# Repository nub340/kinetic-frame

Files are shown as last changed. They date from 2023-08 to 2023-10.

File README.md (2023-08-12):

# Kinetic Frame

## Description
This is an open-source project for building a kinetic art frame. 

The "shredder" variant, mimics the infamous stunt Banksy pulled off at a Sotheby's auction back in 2018. However, where the original device actually shredded the artwork contained within the frame, this one is an illusion. While it really <em>looks</em> like the artwork inside is being shredded, it's actually an artful deception. In reality, a separate pre-shredded copy of the artwork is concealed within the frame, which is cleverly lowered from the bottom of the device while the displayed artwork smoothly scrolls down and out of view, resulting in a very convincing illusion. The device can then be reset to it's original state so the performance can be enjoyed again and again, indefinitely!

The "scroller" variant, is a simplified version that simply scrolls the artwork in a few different ways: 
- Continuously scrolling - Keep scrolling the same direction, continuously.
- Panning - Slowly scroll all the way down, stop, then all the way back up again, stop, repeat.
- Toggle - switch between two different images

The main artwork needs to be printed onto a 13.5" x 36" canvas belt (or similar). The belt is mounted on rollers that are spun by a stepper motor. The "shredder" variant also requires a second copy of the artwork to be mounted to a clip hung from a fishing line. See the assembly instructions for more details.

## Authors
- [nub340](https://github.com/nub340)

## Status   
Alpha release. This is the "first light" push which has been fully built and tested by the original author 

See [CHANGELOG](CHANGELOG.md) for more details
  
<!-- ## See what it looks like
Describe what sets this apart from related-projects. Linking to another doc or page is OK if this can't be expressed in a sentence or two.

**Screenshot**: If the software has visual components, place a screenshot after the description; e.g.,

![](https://blah.png) -->

## Tech Stack & Requirements 
- Arduino
- C++ code/sketch
- Custom PCBs via JLCPCB
- 3D printed parts
- Manual fabrication

## Tools & Cosumables Needed
- Hack saw or power saw for cutting aluminum tubing
- Heat gun or blow dryer for heat shrink tubing
- Soldering iron & solder (heavy and thin rosin core)
- Wire strippers/cutters
- Pliers/crimper
- 3D printer
- JB Weld for Metal (or similar)
- Fabric glue

## Materials Required
Description | Qty | Qty Type | Note
--- | --- | --- | ---
[Arduino Nano](https://www.amazon.com/LAFVIN-Board-ATmega328P-Micro-Controller-Arduino/dp/B07G99NNXL) | 1 | pieces | Microcontroller. The brain of the whole device.
[NEMA17 Stepper Motor](https://www.amazon.com/gp/product/B00PNEQ79Q) | 1 | pieces | Low profile recommended for compactness
[A4988 Driver](https://www.amazon.com/HiLetgo-Stepstick-Stepper-Printer-Compatible/dp/B07BND65C8) | 1 | pieces | Drives the stepper motor
[12V-to-5V Buck Converter](https://www.amazon.com/gp/product/B08Q3TKJH5) | 1 | pieces | 5V for Arduino, A4988 driver, and other components
[IR Remote & Receiver](https://www.amazon.com/DWEII-Infrared-Wireless-Control-Raspberry/dp/B09ZTZQFP7) | 1 | pieces | Any will work, may need to update [code](./Code/banksy_shredder_frame.ino#L16)
[Buzzer](https://www.amazon.com/gp/product/B01N7NHSY6) | 1 | pieces | Active or passive will work. Use resistor with passive.
[Resistor](https://www.amazon.com/Resistor-Tolerance-Resistors-Limiting-Certificated/dp/B08QRT11GG) | 1 | pieces | Optional for Active buzzer. Passive use 100ohm.
[4-Pin Connectors](https://www.amazon.com/CQRobot-Connector-Terminal-Industrial-Integrated/dp/B0731NHS9R) | 1 | pieces | Optional. Can solder motor wires directly to PCB
[1" Aluminum Tubing](https://www.mkmetal.net/6061-t6rndtube1x.065x12) | 28 | inches | Top & bottom rollers. 1" x .065" (ID: .87" \| 22.1mm)
[Skateboard Bearings](https://www.amazon.com/gp/product/B07S1B3MS6) | 3 | pieces | JB Weld flush into ends of aluminum tube
[ Heat Shrink Tubing](https://www.amazon.com/gp/product/B0B38T8SC1) | 2 | pieces | (1.25" Diameter x 15" Length) X 2. Shrink over aluminum tubes to make rollers.
[Motor mount spool](./STL/motor-mount-spool.stl) | 1 | pieces | 3D print. Connects stepper motor to the upper roller, and provides a spool for the fishing line.
[Fishing line](https://www.amazon.com/Zebco-Quantum-300210-Outcast-Monofilament/dp/B000KKUO8S) | 3 | feet | 10lb+ recommended to minimize stretching
[Eye hook screws](https://www.amazon.com/gp/product/B0899QTFWS) | 2 | pieces | 10x5mm. Fishing line routing.
[Swivel hook](https://www.amazon.com/Dr-Fish-Interlock-Stainless-Corrosion-Resistanc/dp/B07JQBLZQG) | 1 | pieces | Optional. Small size 14. Attach fishing line to clip
[Shredded Artwork Clip](./STL/clip.stl) | 1 | pieces | Holds the shredded artwork inside frame
[Roller mount pins: long](./stl/roller-mount-pin-long.stl) | 3 | pieces | 3D print. Top & bottom rollers are mounted and rotate on these.
[Roller mount pins: short](./stl/roller-mount-pin.stl) | 4 | pieces | 3D print. Rubber bands attachments to provide tension on bottom roller.
[3/4" Canvas Offset Clips](https://www.amazon.com/gp/product/B01MS39JJP) | 4 | pieces | For mounting picture frame to completed PCB box
[12V Power Adapter](https://www.amazon.com/gp/product/B00Q2E5IXW) | 1 | pieces | Minimum 2A for stepper motor. 8ft cord recommended
[Barrel Connector](https://www.amazon.com/gp/product/B074LK7G86) | 1 | pieces | Connection for 12V power adapter
[Paper Mount Boards](https://www.dickblick.com/items/crescent-mounting-board-15-x-20-x-055-ultra-black)  | 2 | pieces | For internal separator and back pieces. [Cut to size](#mount-boards).
[Card Stock](https://www.amazon.com/gp/product/B0773KWZLG) | 1 | pieces | Optional backing. Glue to back of artwork copy before shredding for better support and durability.
[12" x 16" Picture Frame](https://www.etsy.com/listing/630386658/west-frames-elegance-french-ornate) | 1 | pieces | Minimum 1-1/2" Moulding to hide motor & electronics
[Custom PCB: Left & Right](./PCB/Gerber_Left_Right.zip) | 1 | pieces | Order from [JLCPCB](https://jlcpcb.com/)
[Custom PCB: Top, Bottom, & Supports](./PCB/Gerber_Top_Bottom.zip) | 1 | pieces | Order from [JLCPCB](https://jlcpcb.com/)
[Main Artwork Canvas: 13.5" x 36"](https://www.bagsoflove.com/unframed-canvas-photo-prints) | 1 | pieces | The main un-shredded artwork that will be displayed in the frame.
[Shredded Artwork Canvas: 13.5" x 12 - 16"](https://www.bagsoflove.com/unframed-canvas-photo-prints) | 1 | pieces | The shredded artwork that will be lowered from the bottom of the frame. Doesn't have to be full 16" as only around half is ever exposed.

## Getting the Printed Circuit Boards (PCBs) Made
You can have the PCBs made via JLCPCB. They require a minimum of 5 copies of any PCB. Follow the steps below to order:

- Browse to [JLCPCB](https://jlcpcb.com/)
- Click "Instant Quote" button
- Upload [Gerber file for Left & Right](./PCB/Gerber_Left_Right.zip) pieces
- Under the <b>PCB Specifications</b> section, select the following:
    - <b>Different Design</b>: ```2```
    - <b>Delivery Format</b>: ```Panel by Customer```
    - <b>PCB Thickness</b>: ```2.0```
    - <b>PCB Color</b>: <em>Select your desired color</em>
- Click "Save to Cart".
- Repeat for [Top, Bottom, and Supports](./PCB/Gerber_Top_Bottom.zip) Gerber file
    - Only difference is choose <b>Different Design</b>: ```3``` this time
- You will end up with 2 items in your cart. Proceed to checkout when you are ready to place your order.
- You can choose ```1.6``` PCB thickness to save money, but ```2.0``` is way sturdier and recommended.
- <b>NOTE</b>: ```Gerber files are just zip files. Upload the whole zip, no need to extract first.```

## Fabricating the Rollers
You'll need to fabricate the upper & lower rollers from a few components:
- Aluminum tubing
- Skateboard bearings
- Heat shrink tubing
- JB weld for metal/aluminum (marine works well)

Follow these steps:
- Cut the aluminum tubes to length:
    - Upper: ```13-3/4"``` (extra space needed for 3D printed motor mount spool)
    - Lower: ```14"```
- Install bearings:
    - You'll need three bearings total. One for the upper, and two for the lower.
    - Test fit the bearings into the ends of the tubes. Make sure they will fit nice and flush with the ends of the tubes. You may need to sand the inside of the tubes slightly if it's too tight a fit.
    - Remove all three bearings.
    - Install one bearing at a time with the following procedure:
        - Apply/scrape a <em>little bit</em> of JB weld all around the inside perimeter of the tube openings such that when the bearing is pressed in, it will make contact with both the outer bearing race and inner tube wall. 
        - Press bearing into tube end so that it sits nice and flush with the tube end.
        - Don't use too much JB Weld as you don't want it to get onto the inner bearing race.
        - Let the JB Weld harden/cure thoroughly.
        - Ensure the bearing spins freely. See [notes](#bearing-notes) below if not.
- Apply heat shrink:
    - Cut two ~15" lengths of heat shrink tubing and shrink them onto each roller, both upper and lower.
    - Trim the excess heat shrink tubing with a razor blade so that it's perfectly flush with the ends of the tubes and bearings, with no overhang.
- Install 3D printed motor mount spool
    - Press into the tube opening opposite of the bearing of the upper roller tube
    - Ensure that it is fully pressed in and seated so that it grips the tube well.
    - Total length of tube plus motor mount should be 14" 

NOTES:

- If you get JB Weld on the center bearing race and it doesn't want to spin, you can try to use your finger, or stick a large pen or something similar through the hole until it grabs onto the sides of the hole, and then spin the tube to try and break bond and get it spinning freely.
- You might be able to use PVC tubing instead of aluminum, but the PVC might warp when applying the heat shrink tubing.
- If you got the right tubing and skateboard bearings, they should fit right into the ends of the tubes. The outer diameter of the bearings are 22mm, so the inside diameter of the tubes need to be just over 22mm.

## Fabricating the Artwork
The shredder frame requires two separate copies of the same artwork to function. One for the main un-shredded art that will be visible in the frame when in the default/normal state, and one for the shredded piece that is lowered from the frame.

The two artworks can be fabricated in many ways so feel free to experiment with different approaches. If you find one that works well that is not covered here, please write up an addendum ```.md``` and make a pull request for it to be included in the main repository.

I have tried a few different approaches myself and found having the canvas made via a service like [bagsoflove](https://www.bagsoflove.com/unframed-canvas-photo-prints) provides the best results. The artwork is printed directly onto a high quality canvas which looks great, and avoids any issues with the picture starting to come off after repeated times going around the rollers.

Gluing a separate artwork onto a blank piece of canvas or vinyl is another (cheaper) approach, but presents potential peeling issues as it must be able to rotate around the lower roller over and over again. If it starts to peel off, it will inevitably start causing jams. I had decent results using a piece of vinyl instead of canvas and using a high strength 3M spray adhesive.

You can also simply make your own stencils and spray paint directly on a blank canvas, although this might be harder to make two identical copies.

### Main Un-shredded Artwork
- 13.5" x 36" made into a belt/loop
- Mounted on rollers
- Have made
    - https://www.bagsoflove.com/
    - https://www.contrado.com/
    - You'll need to upload a high quality image (i.e. 200 DPI) in the right dimensions.
    - [Example image](./Images/banksy_13.5x52_fiberboard_200DPI.png)
        - Single image contains both the un-shredded (upper) and shredded (lower) artworks in one. 
        - It will be delivered as one big canvas, so you'll need to separate the upper and lower canvases by cutting with scissors or fabric cutter, etc. Cut very precisely along the horizontal dotted line separating the upper and lower portions.
        
        - cut the bottom image out and glue it to cardstock before manually shredding for best results and durability. 
        - Only shred bottom half of shredded artwork canvas.
        - Trim the upper un-shredded artwork canvas so that it's 13-1/2" wide, and ~37" tall. Use high quality fabric glue to make into a belt/loop. You only need about an inch of overlap for glue to make a good bond. 
        - The fiberboard-like background on the upper canvas should loop around and perfectly match with the top to make a perfect 36" long belt. 
- Make yourself
    - Print, Stencil, or Glue artwork onto a 13.5" x 36" canvas about 3/4 of the way down. 
    - Make into a "belt" by gluing the ends together. 
    - Seam should be near the bottom in back when artwork is centered in frame on the rollers. Far enough down so that it never reaches the upper roller when in the fully shredded state.

## Fabricating the Shredded Artwork
Duplicate artwork above. Glue canvas to cardstock for best results, or just use the cardstock. Shred bottom 50% or so. By hand or with a paper shredder you can stop & reverse.

## 3D Printed Parts
- [Motor mount spool](./STL/motor-mount-spool.stl) - Connects the motor to the upper roller. Also provides a spool for the fishing line and acts as a winch for lowering and raising the shredded artwork hidden inside.
- [Roller mount pin: long](./STL/roller-mount-pin-long.stl) - Provides a spindle for the upper & lower rollers to mount and rotate on.
- [Roller mount pin: short](./STL/roller-mount-pin.stl) - Provides an attachment point for the tensioning rubber bands for the lower roller.
- [Artwork clip](./STL/clip.stl) - Provides an attachment point for the shredded artwork to hang from. 

It's recommended to print these components with PETG or PLA @ .15mm or better resolution and 15% infill. Be sure to use the appropriate slicer for your printer. 

## Mount Boards

- Separator: 14.25" x 18.25" 
- Backing: 14.5" x 18.75"
    - bend the bottom slightly so that the shredded artwork is pushed away from the wall a little

## Known issues

Calibration

----

## Open source licensing info
1. [TERMS](TERMS.md)
2. [LICENSE](LICENSE)
3. [CFPB Source Code Policy](https://github.com/cfpb/source-code-policy/)

----

## Credits and references

1. Banksy for his original performance art
2. Creative engineers
3. Arduino

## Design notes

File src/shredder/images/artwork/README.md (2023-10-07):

Images in this folder are intended to be used for printing onto a canvas 13.5" x 52" in size and includes two copies of the same image. Cut them at the seam to make a 36" upper and a 16" lower canvas.

Form the upper 36" canvas into a loop/belt by gluing or sewing the top and bottom together. You want the loop/belt to be 36" in circumference, so don't overlap the actual printed portion. Use the non-printed margin for any overlap. Better yet, sew the two ends butted up against each other with no overlap at all.

It is recommended to glue the lower 16" canvas to cardstock or thick paper for durability and to prevent fraying. You can cut it shorter than 16" but you'll need to adjust the length of the fishing line to compensate.

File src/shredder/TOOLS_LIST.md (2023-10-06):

# Tools, Equipment, and Software List

- Soldering Iron
- 1.5mm Allen Wrench
- Pliers
- Philips Screwdriver
- Computer with Internet Access
- Arduino IDE
- USB Cable (micro or type-C, depends on the Arduino Nano you got)
- 3D Printed 90-Degree Jig

## Consumables
- Solder (thick rosin core)
- Solder (thin rosin core)
- Tape (masking, painters, or scotch)
- Epoxy, JBWeld, Silicone, or Glue

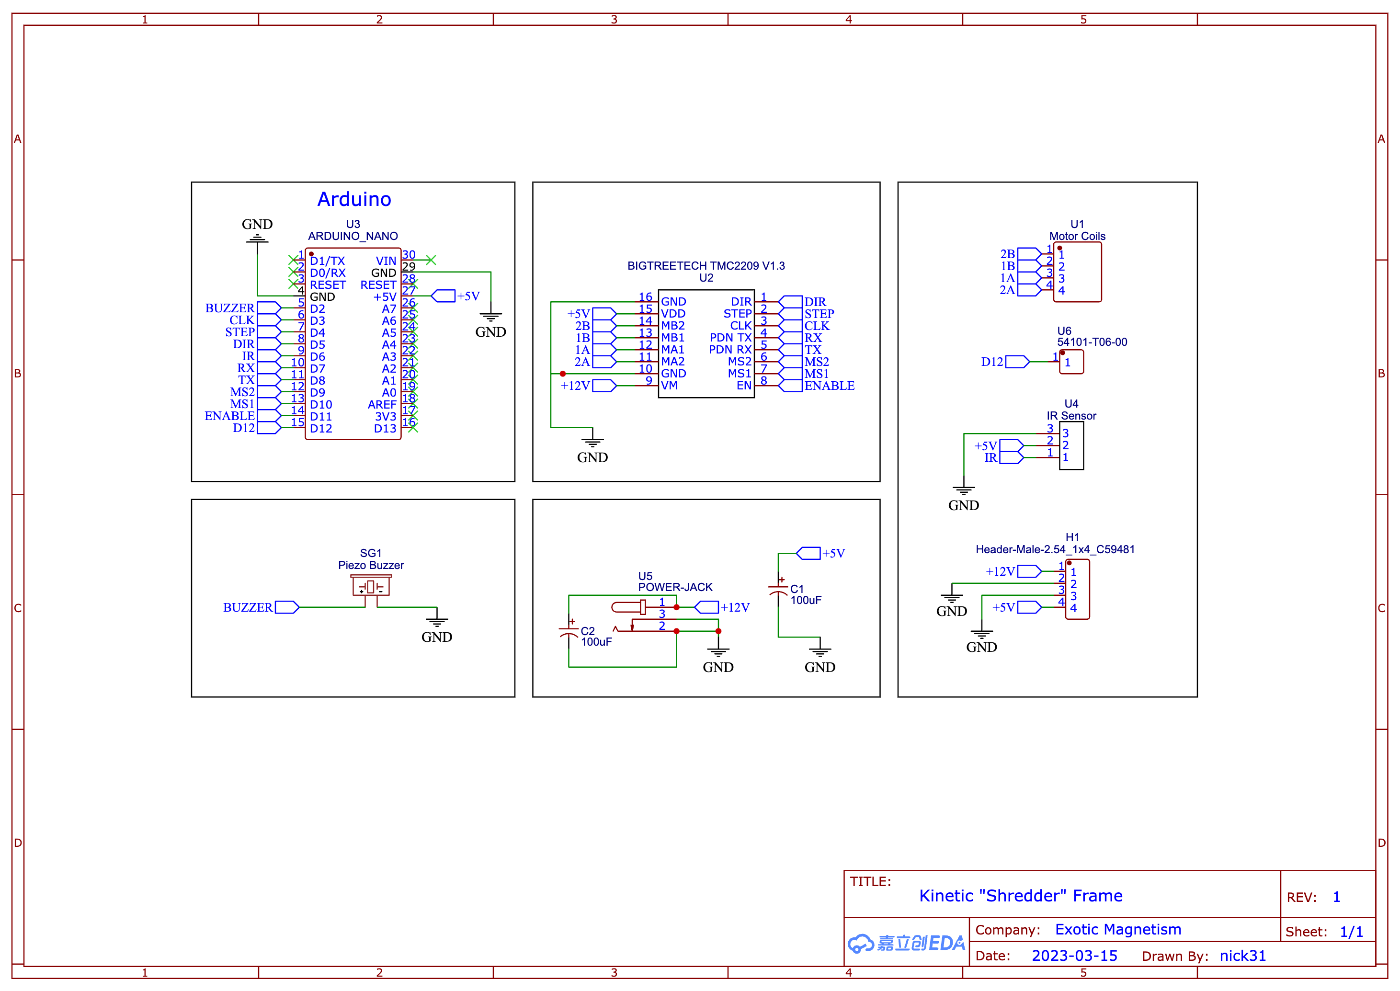
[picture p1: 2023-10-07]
src/shredder/pcb/Schematic_TMC2209.png

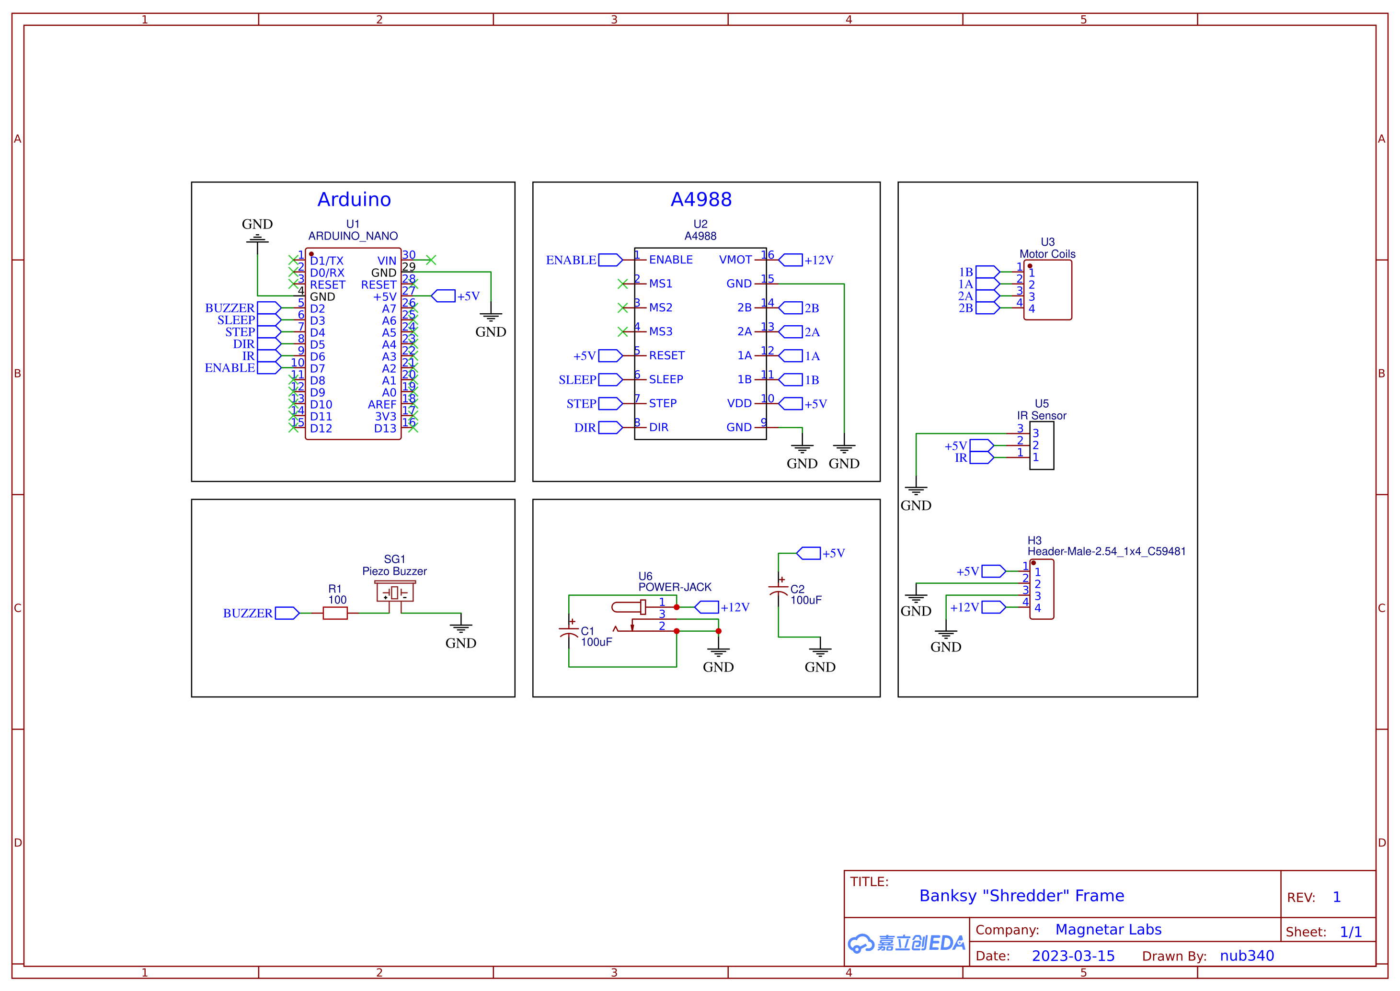
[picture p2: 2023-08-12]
src/shredder/pcb/Schematic_A4988.png

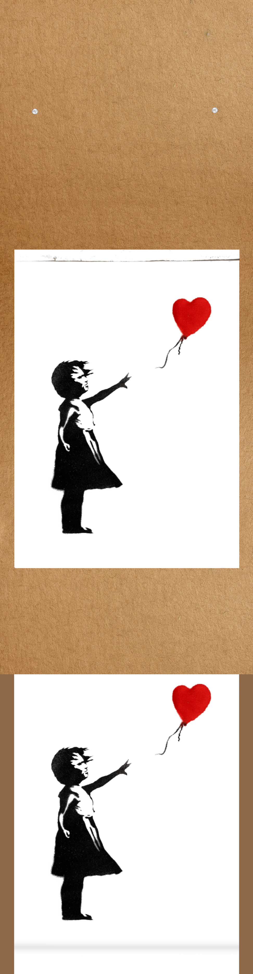
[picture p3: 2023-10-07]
src/shredder/images/artwork/banksy_13.5x52_fiberboard.jpg

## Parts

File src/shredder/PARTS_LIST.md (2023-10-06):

# Parts List

## Structural
- PCB Frame (Left, Right, Top, Bottom)
- Aluminum Tubing (x2)
- Heat Shrink Tubing (x2)
- Flanged Bearings (x3)
- 3D Printed Bearing Mounting Pins (x3)
- 3D Printed Motor Mount
- Eyelets (x3, 1 needed, 2 extra)
- Small Rubber Bands (x8)
- Fishing Line
- Swivel Hooks (x2)
- 3D Printed Hanger
- Art Board (x2)
- Rubber Bands (x8)

## Electronics
- Arduino
- Stepper Motor Driver (A4988 or TMC2209)
- 5V Buck Converter
- 4-pin Header
- IR Receiver
- Piezo Buzzer
- 100uf 16v Capacitors (x2)
- Barrel jack
- Stepper Motor Pigtail

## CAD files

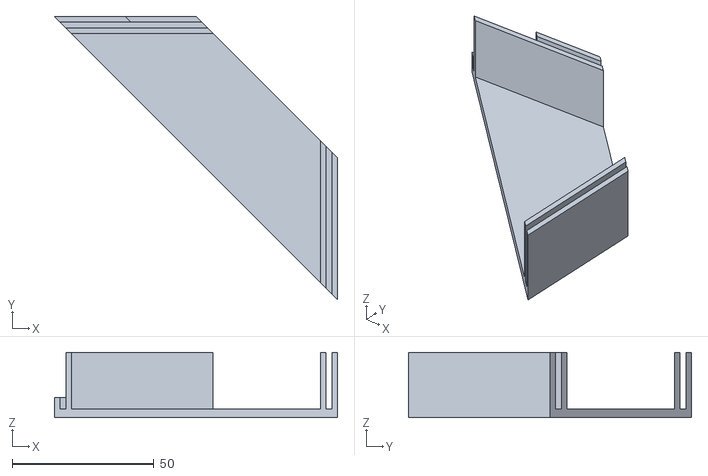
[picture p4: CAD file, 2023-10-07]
src/shredder/3dprint/90degree-jig2.stl
100.0 x 100.0 x 23.0

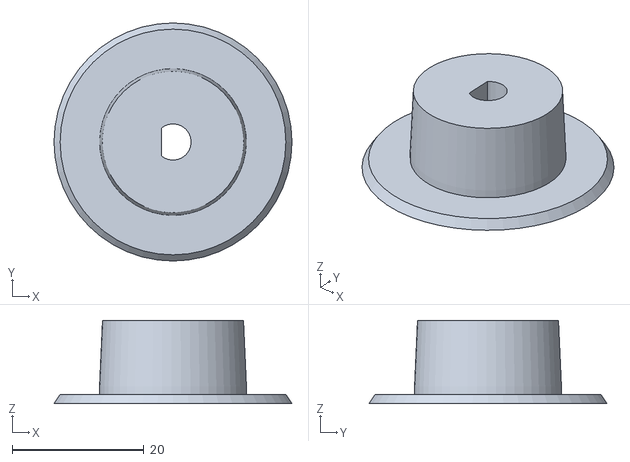
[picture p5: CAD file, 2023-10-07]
src/shredder/3dprint/motor-mount.stl
36.1 x 36.1 x 12.6

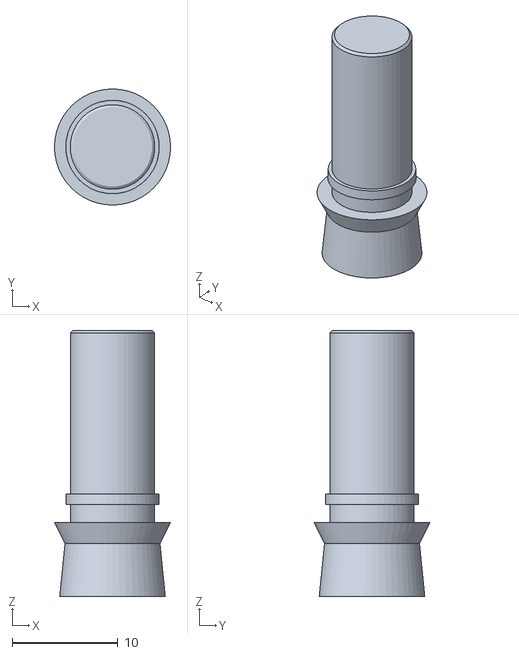
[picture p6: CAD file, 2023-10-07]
src/shredder/3dprint/roller-mounting-pin.stl
11.0 x 11.0 x 25.2

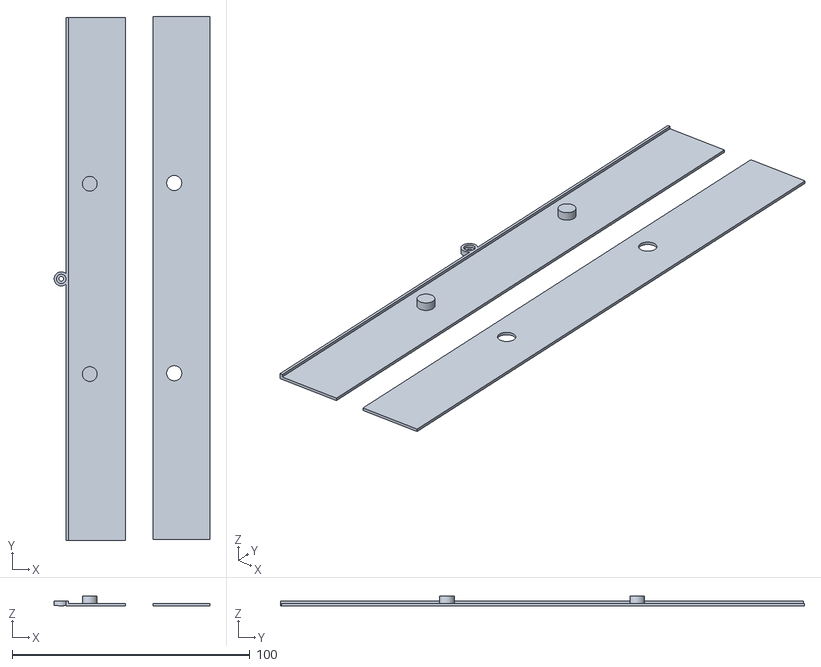
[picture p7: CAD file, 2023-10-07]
src/shredder/3dprint/hanger.stl
65.5 x 220.3 x 4.00

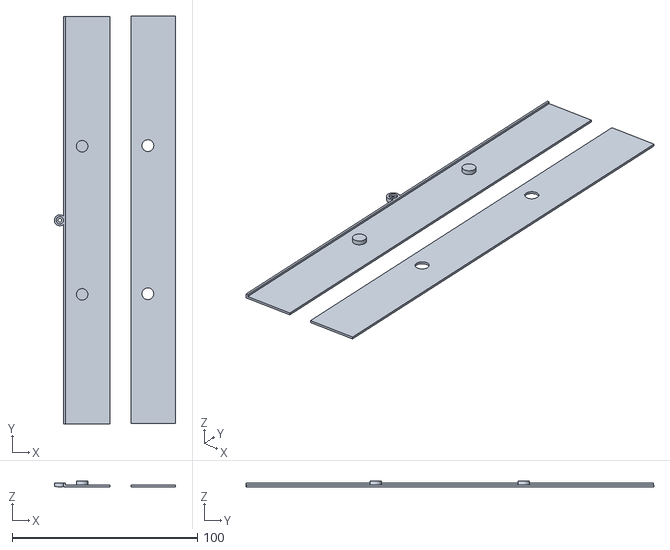
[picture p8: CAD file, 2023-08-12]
src/shredder/3dprint/clip.stl
65.5 x 220.3 x 3.00

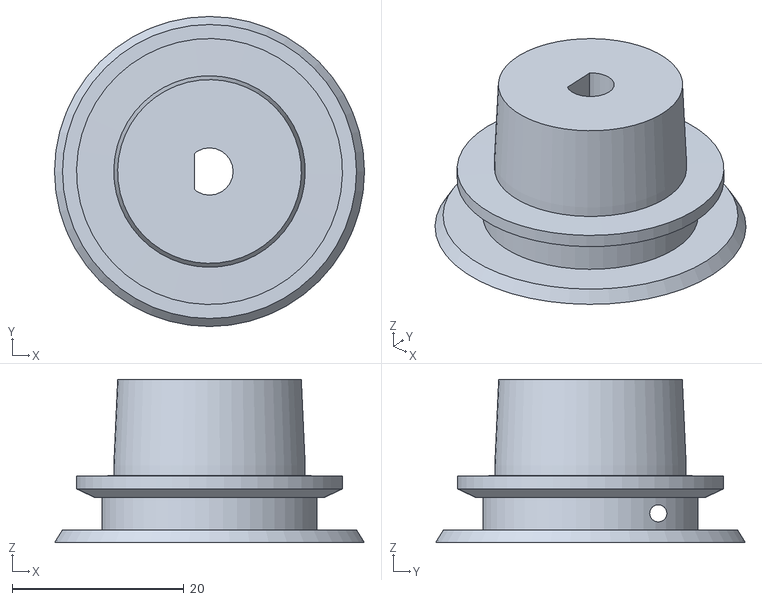
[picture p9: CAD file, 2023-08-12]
src/shredder/3dprint/motor-mount-spool.stl
36.1 x 36.1 x 19.0

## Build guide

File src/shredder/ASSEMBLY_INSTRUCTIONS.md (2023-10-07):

# Kinetic Shredder Frame Kit Assembly Instructions

### Prerequisites
Ensure that you have all of the parts and tools on hand before continuing.

- [Parts](PARTS_LIST.md)
- [Tools](TOOLS_LIST.md)

## 1. Assemble the PCB chassis
Use the included 3D printed jig to position the PCB pieces so their corners meet at a 90 degree angle.

### Tools Required
- 90 Degree Jig
- Soldering Iron
- Solder (thick rosin core)

### Parts Needed
- "Left" PCB
- "Right" PCB
- "Top" PCB
- "Bottom" PCB
- Lateral Support PCBs (x3)

### Steps
- The PCBs come in two panels. Break them apart carefully into their constituent pieces.
- Join the "Left" and "Top" PCB pieces first.
    - Place both pieces in the jig so that the sides marked "Front" are facing the same direction.
    - Carefully bring the corners together so that the tabs interlock and fit together with no gaps and a nice 90 degree angle is achieved.
    - The silver metal strips should be facing each other on in the inside of the corner.
    - Cut a piece of rosin core solder and lay it in the corner on the silver metal strips.
    - Use your soldering iron to melt the solder to join the "Left" and "Top" PCB pieces together.
    - Let it cool before attempting to remove from jig.
- Join the "Left" and "Bottom" PCB pieces
- Join the "Right" and "Top" PCB pieces
- Join the "Right" and "Bottom" PCB pieces
- Install the three lateral support pieces
    - Start with the middle support
    - Use a pice of tape to hold the "Left" and "Right" PCB pieces at the correct distance so that the ends of the middle support are flush with the exterior
    - solder both sides and let cool
    - flip over, solder both sides again and let cool
    - Repeat for the top and bottom lateral supports

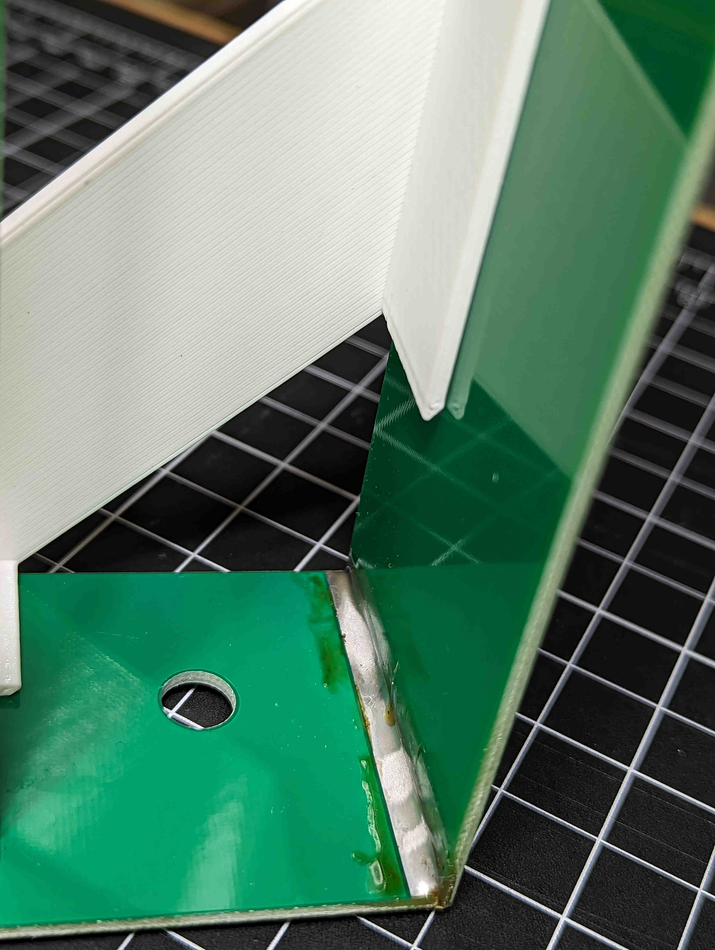
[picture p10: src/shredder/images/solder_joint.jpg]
solder joint

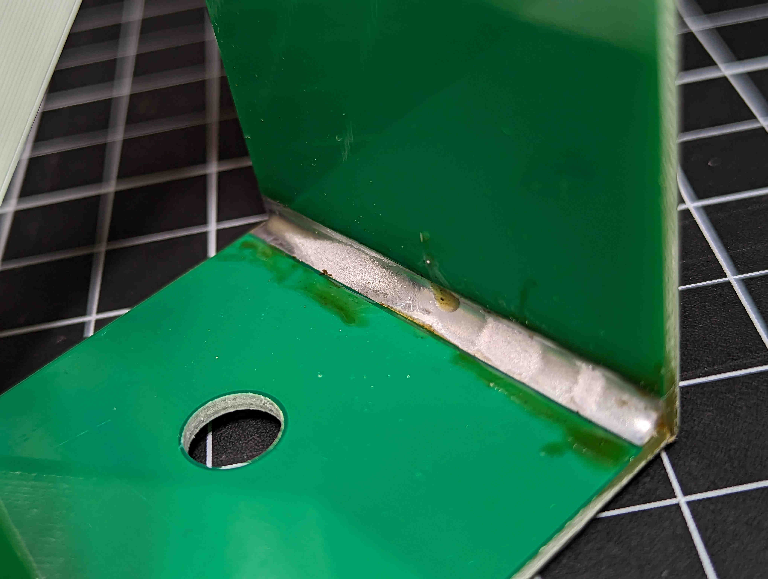
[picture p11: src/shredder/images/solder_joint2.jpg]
solder joint closeup

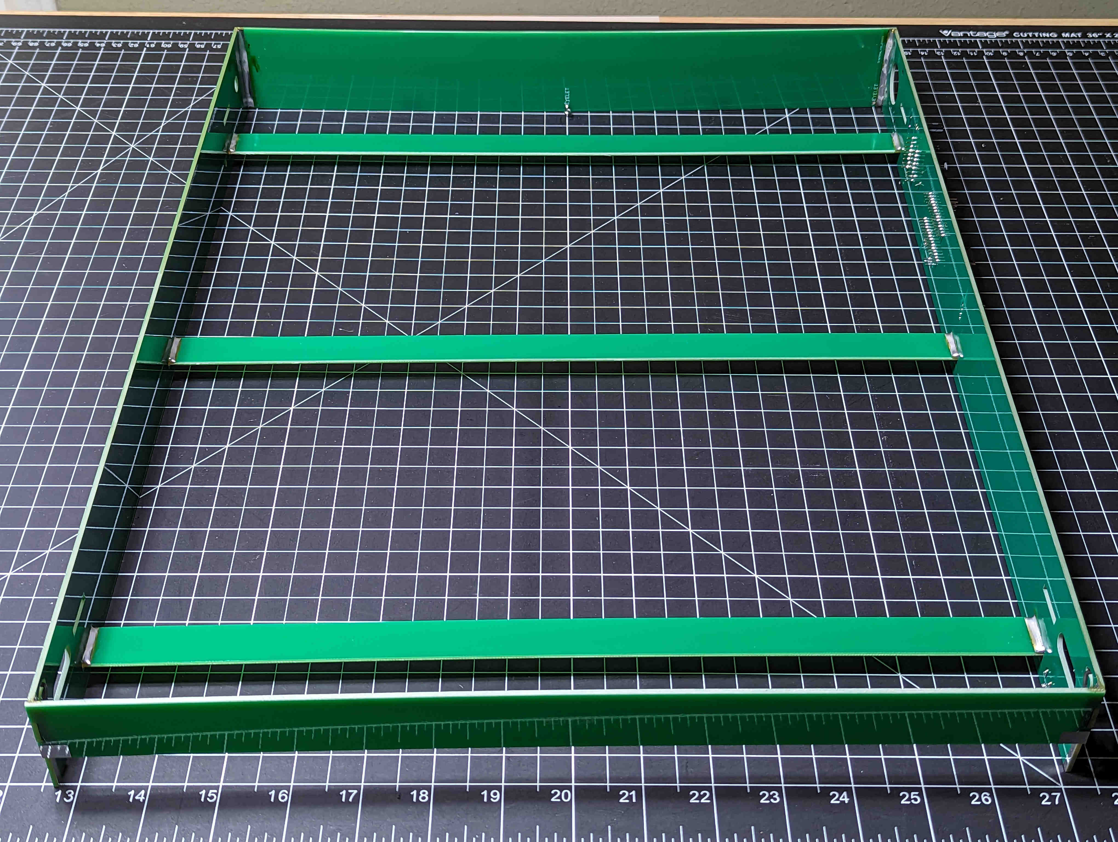
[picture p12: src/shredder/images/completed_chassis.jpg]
completed chassis


## 2. Install the eyelet
The eyelet is used as a pulley of sorts for the fishing line that will hold the pre-shredded image within the chassis.

### Tools Required
- Pliers
- Soldering Iron
- Solder (thin rosin core)

### Parts Needed
- Eyelet
- Chassis

### Steps
- Install the small eyelet into the hole located at the center rear of the "Top" PCB piece.
- The eyelet is fragile and can easily break, so don't screw it in more than one or two turns. Just enough so that it stays in place. It should NOT need to poke through the top. 
- Orient the eyelet hole so that it's facing front & back. 
- Use a dab of solder on top & bottom to secure it in place.

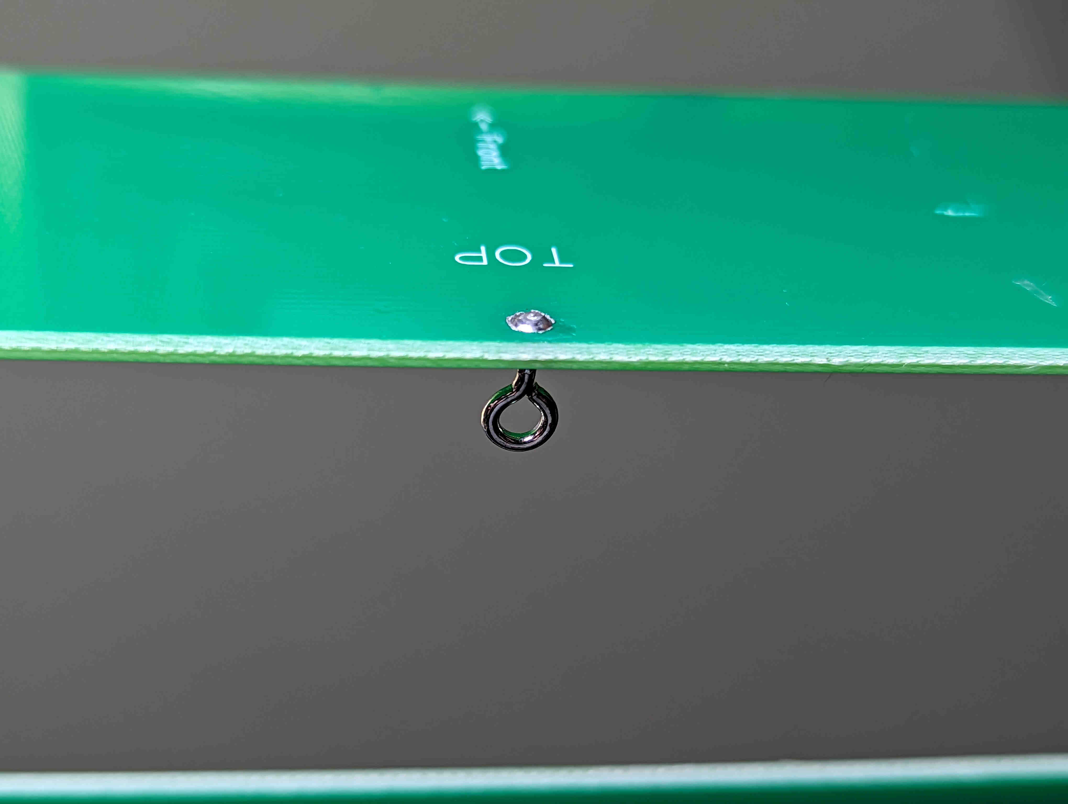
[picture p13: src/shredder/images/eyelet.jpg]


## 3. Solder the Electronics
Install and solder all of the electronic components on the PCB labeled "Right". Be sure to pay attention to the orientation of each component to ensure the pins and polarity are correct.

### Tools Required
- Soldering Iron
- Solder

### Parts Needed
- Arduino
- Stepper Motor Driver (A4988 or TMC2209)
- 5V Buck Converter
- 4-pin Header
- IR Receiver
- Piezo Buzzer
- 100uf 16v Capacitors (x2)
- Barrel jack
- Stepper Motor Pigtail

### Steps
- Arduino 
- Stepper Motor Driver 
- Active Piezo Buzzer 
- Capacitors 
- 12V Barrel Jack
- 4-pin Header
    - Buck Converter goes onto 4-pin Header
    - When oriented correctly, should hang downwards
    - EN pin does not connect to anything
- IR Receiver
- Stepper Motor Pigtail
    - From left to right (front to back): Red, Blue, Green, Black
    - DO NOT INSTALL THE STEPPER MOTOR ITSELF YET

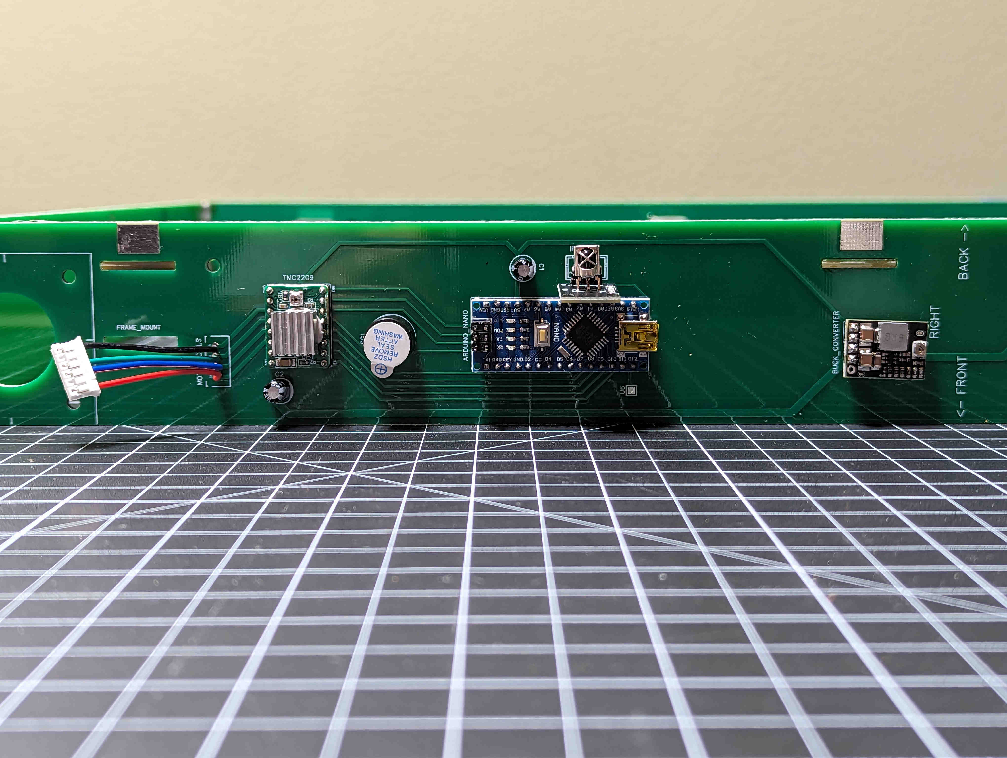
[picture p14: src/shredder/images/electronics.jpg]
electronics

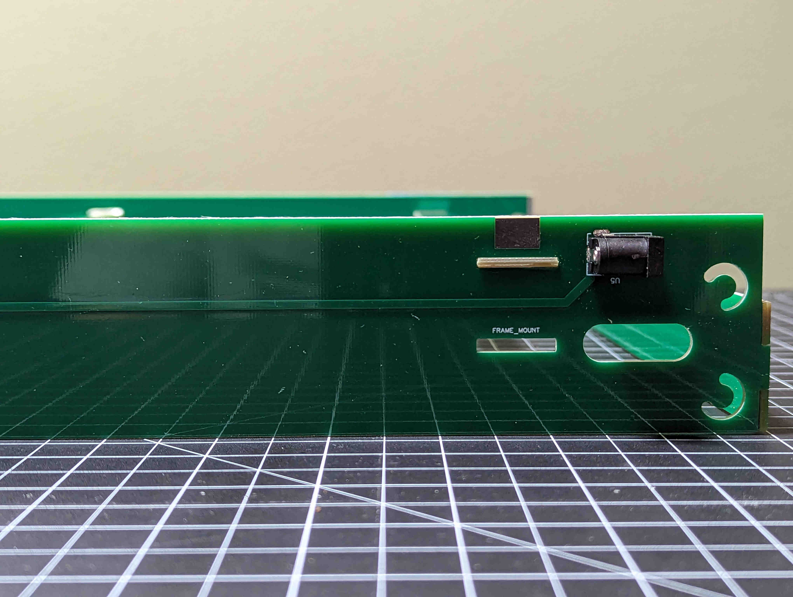
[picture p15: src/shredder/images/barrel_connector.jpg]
barrel connector


## 4. Construct the Rollers
The rollers are made from aluminum tubing and some heat shrink to make a rubberized surface for better grip. Bearings and a motor mount are used in the ends.

### Tools Required
- Heat Gun or Hair Dryer
- Epoxy/JBWeld/Silicone/Glue (optional)

### Parts Needed
- Aluminum Tubes (x2)
- Heat Shrink Tubing (x2)
- Flanged Bearings (x3)
- Motor Mount

### Steps
- Apply heat shrink to both tubes
    - Place an aluminum tube through a piece of heat shrink tubing. There should be a little overhang at each end.
    - Use a heat gun or blow dryer to shrink the tubing onto the tube until it's uniformly tight and smooth
    - Cut the excess tube overhanging the ends so that it is flush with the ends
- Top Roller
    - Pick one roller to be the top roller. It doesn't really matter which one as they are the same length. 
    - Insert a flanged bearing into one end, and the motor mount into the other
    - Ensure you press them all the way on and check that they fit tightly
    - If they don't fit tightly you can use some epoxy, silicone, or glue, but this is optional.
- Bottom Roller
    - Install a flanged bearing into each end. 
    - If they don't fit tightly and fall out easily you can use some silicone, or epoxy, or any kind of glue really.
- If you used some sort of glue, let it dry thoroughly before continuing.

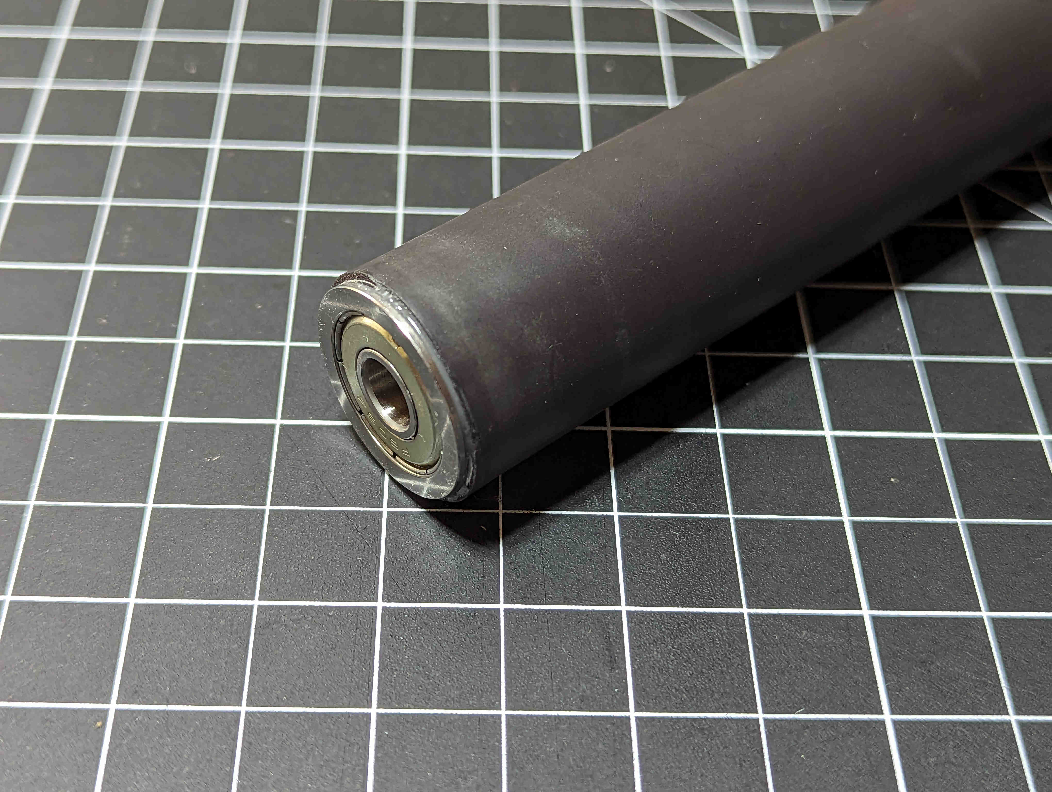
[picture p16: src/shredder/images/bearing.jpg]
roller bearing

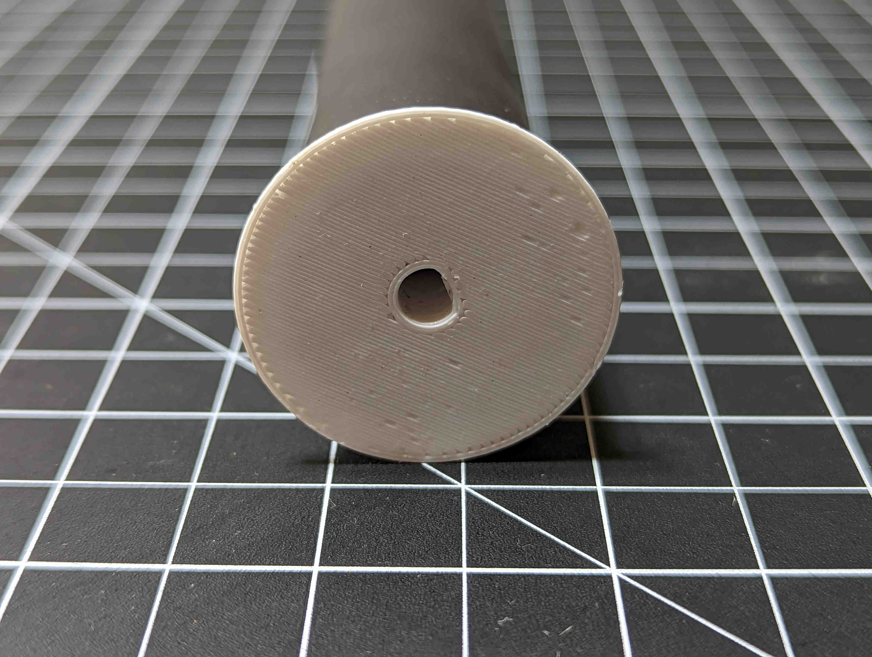
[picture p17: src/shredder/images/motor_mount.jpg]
roller motor mount

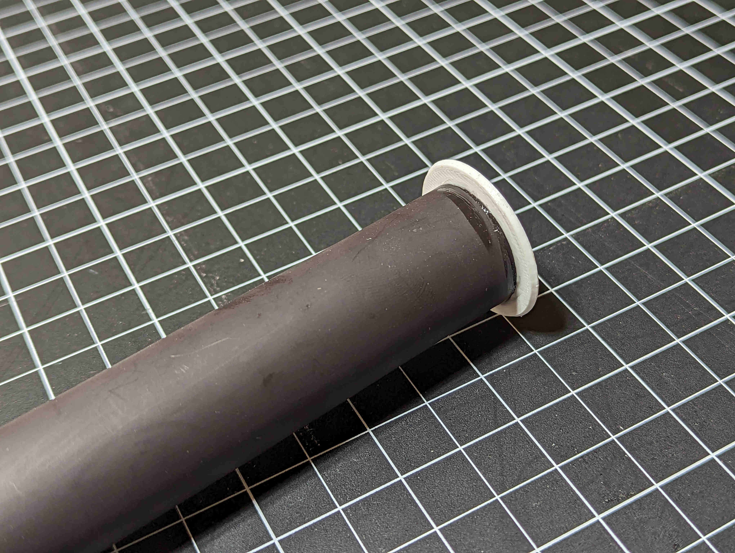
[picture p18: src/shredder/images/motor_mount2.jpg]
roller motor mount


## 5. Install rollers, canvas belt, and motor
You need to install the rollers, canvas belt, and motor all at the same time.

### Tools Required
- 1.5mm allen wrench
- Tweezers (optional)

### Parts Needed
- Top Roller Assembly
- Bottom Roller Assembly
- Canvas Artwork Belt
- Stepper Motor
- Roller Mounting Pins (x3)
- 1.5mm button head screws (x4)
- Rubber Bands (x4)

### Steps
- Place the chassis on a flat surface with the side marked "Front" facing up towards you.
- Place the artwork canvas belt in the frame with the image facing up and centered vertically in the chassis
- Place the top and bottom rollers inside the top and bottom of the canvas belt
- Insert the bottom roller mounting pins through the bottom slot and into the bearing holes on each side
    - The pins should snap into place and stay retained within the slot
- Insert the stepper motor through the chassis and into the motor mount on the right side of the top roller. Ensure the flat side of the hole lines up with the flat side of the motor shaft 
    - You can insert a screw or two to keep the motor in place but don't tighten fully yet
- Insert the remaining roller mounting pin on the left side of the top roller
    - This pin should snap into place as well, however it can take more effort. Be careful not to push too hard on the PCB frame during this part. Try to keep pressure between the back of the motor, tube, and mounting pin only.
- Install and tighten the remaining screws to hold the motor in place.
- Install a couple of rubber bands on each side of the lower roller to provide some tension. You can add more later if needed.
    - Use a pair of tweezers from behind to get the rubber bands on if you're having trouble.

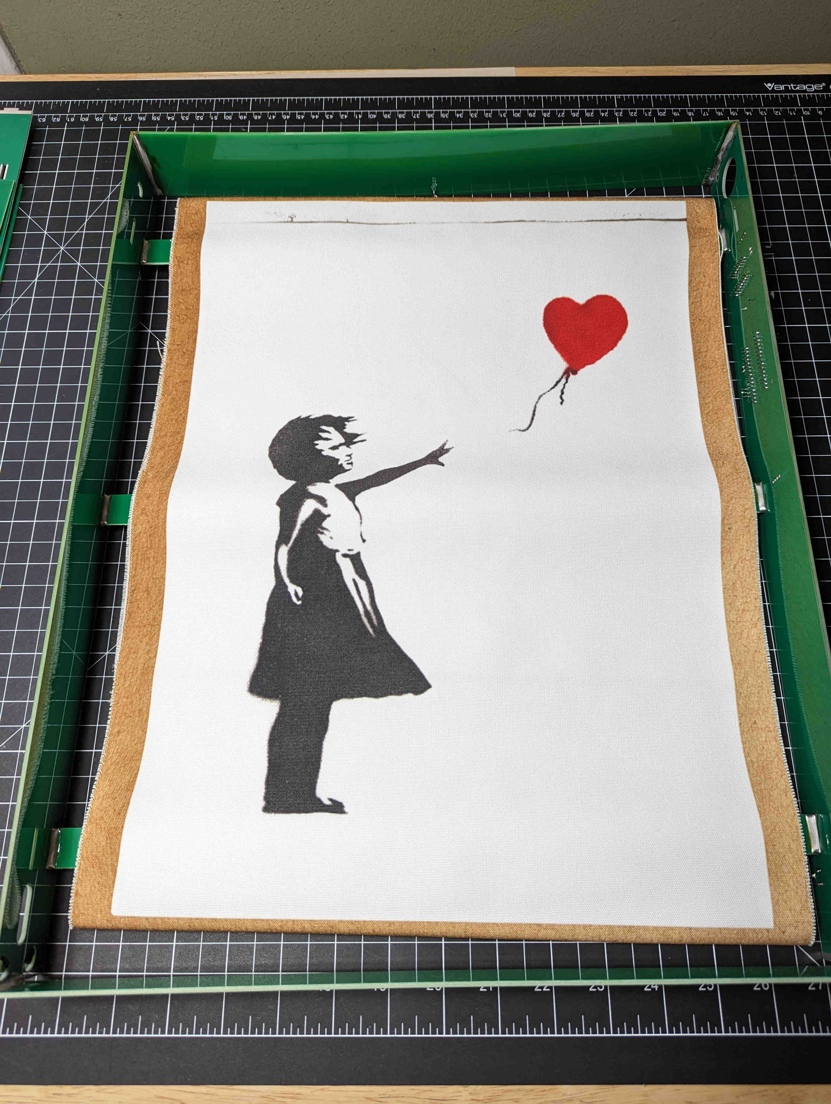
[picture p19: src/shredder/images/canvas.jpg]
position canvas for mounting

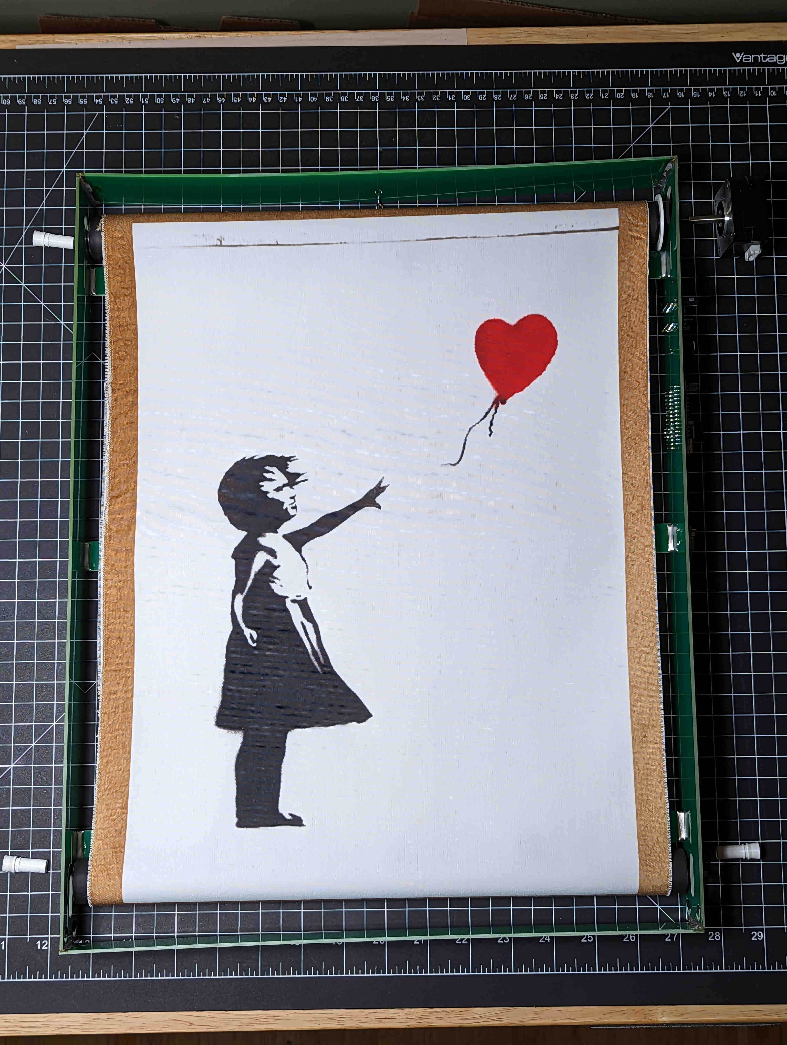
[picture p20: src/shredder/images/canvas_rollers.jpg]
position rollers for mounting

canvas & rollers fully mounted
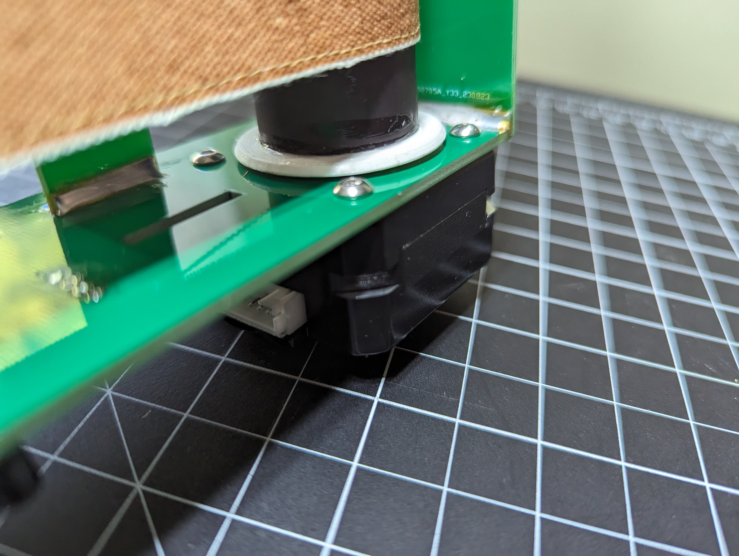
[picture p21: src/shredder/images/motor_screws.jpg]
stepper motor screws

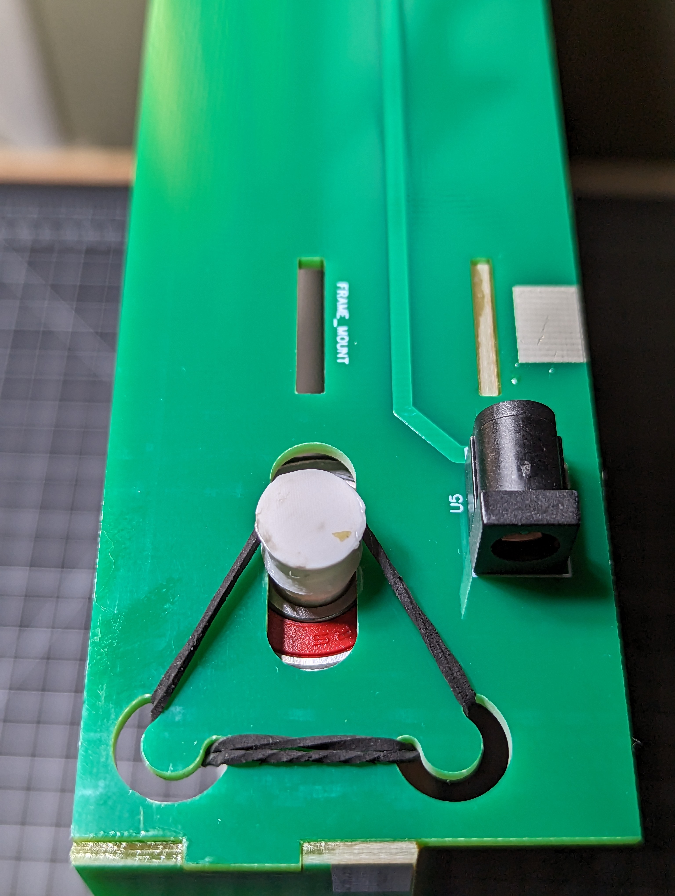
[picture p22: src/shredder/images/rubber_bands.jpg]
tension rubber bands


## 6. Program Arduino
Now lets program the arduino and test that everything is working so far.

### Tools Required
- Computer
- Arduino IDE
- USB cable

### Parts Needed
- Chassis with electronics fully soldered

### Steps
- Download the [initialize.ino](arduino/initialize/initialize.ino) file
- Open the **initialize.ino** file in the Arduino IDE
- Plug the Arduino into your computer via USB
- In the Arduino IDE:
    - Click *Tools* | *Board* | *Arduino AVR Boards* | ***Arduino Nano***
        - You may need to add the board first via the *Boards Manager*
    - Click *Tools* | *Processor* | ***ATmega328P (Old Bootloader)***
    - Click *Tools* | *Port* | ***\<Select the Serial Port for your Arduino>***
    - Click *Tools* | ***Serial Monitor***
        - If port connection is successful a serial monitor window should open
    - Click the ***Verify*** button on the code window toolbar
        - Continue when you see a "Done Compiling" message at the bottom
    - Click the ***Upload*** button on the code window toolbar
        - This will start the process of programming the Arduino
        - When done you should see a message on the Serial Monitor that says something like:
            - **Muted: 0, Shredded: 0, Location: 0**
        - If you see this message, that means that you successfully connected to and programmed the Arduino Nano using the initialize.ino file. This file initializes and persists the starting state of the shredder frame to the internal flash storage.
        - If you get an error, double-check everything and try again.
- Download the .ino file for the stepper motor driver in your kit
    - [A4988](arduino/kinetic_shredder_A4988/kinetic_shredder_A4988.ino)
    - [TMC2209](arduino/kinetic_shredder_TMC2209/kinetic_shredder_TMC2209.ino)
- Open the A4988 or TMC2209 .ino file in the Arduino IDE 
    - Click the ***Verify*** button on the code window toolbar
        - Continue when you see a "Done Compiling" message at the bottom
    - Click the ***Upload*** button on the code window toolbar
        - This will start the process of programming the Arduino
        - You will overwrite the previous initialize.ino code, but the state you persisted to flash will remain intact
        - When done you should see a message indicating that it is running and also show you the current state again.
        - If you see this message, great job. We are done with the programming. Unplug everything for now and move on to the next step.

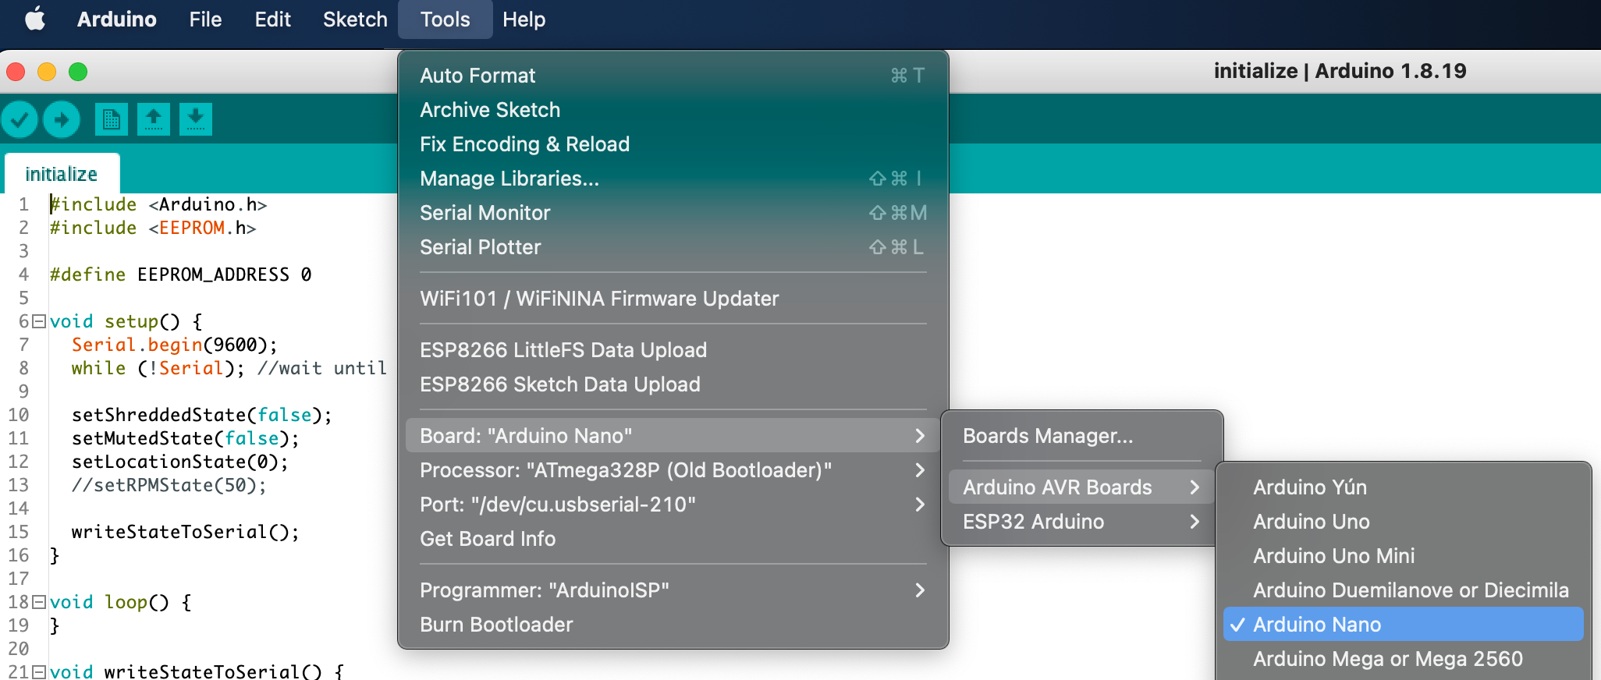
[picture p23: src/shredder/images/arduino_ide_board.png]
arduino ide board

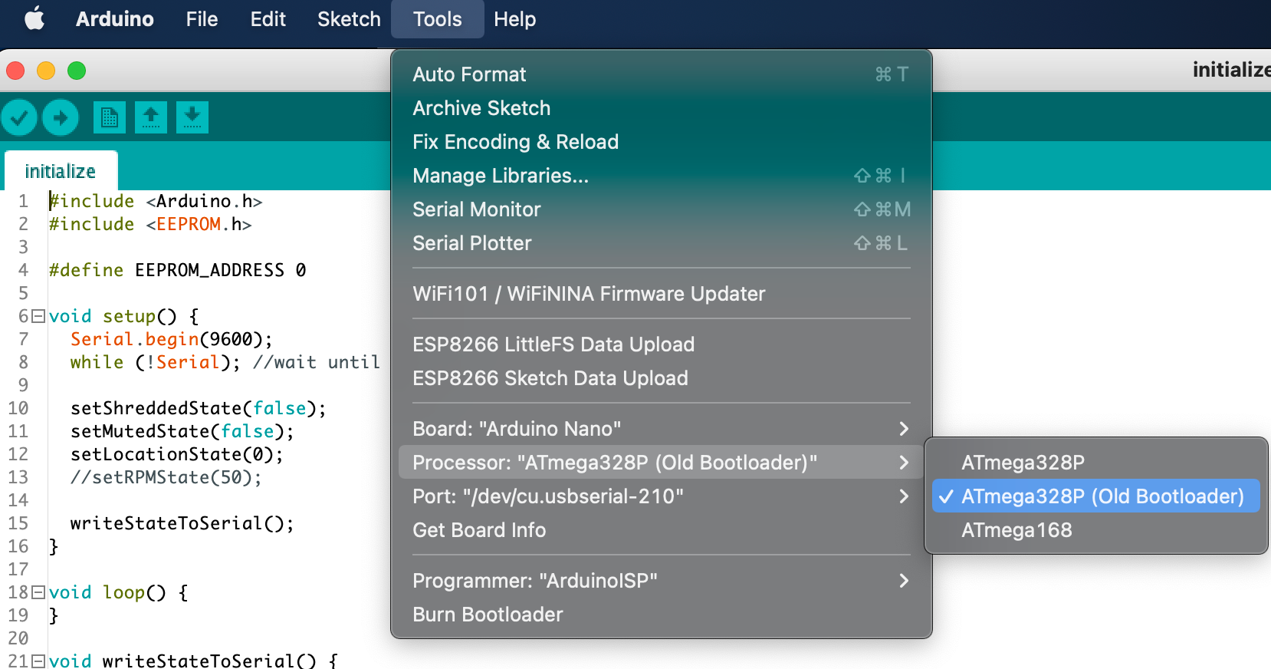
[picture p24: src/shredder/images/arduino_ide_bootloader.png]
arduino ide bootloader

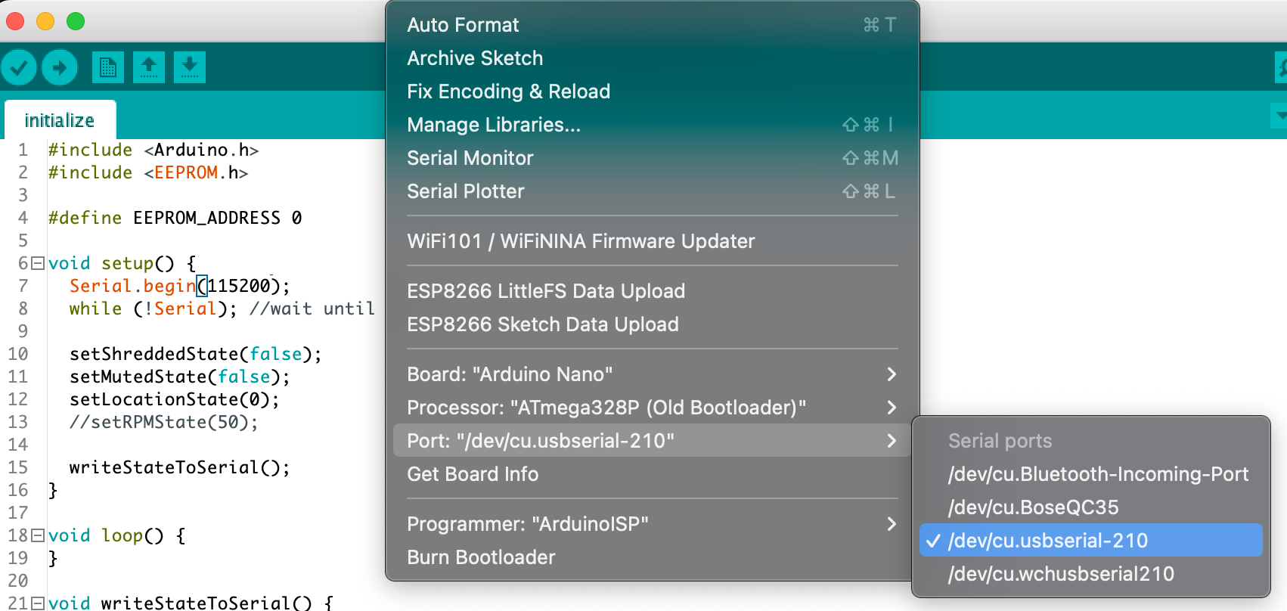
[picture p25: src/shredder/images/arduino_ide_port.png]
arduino ide port

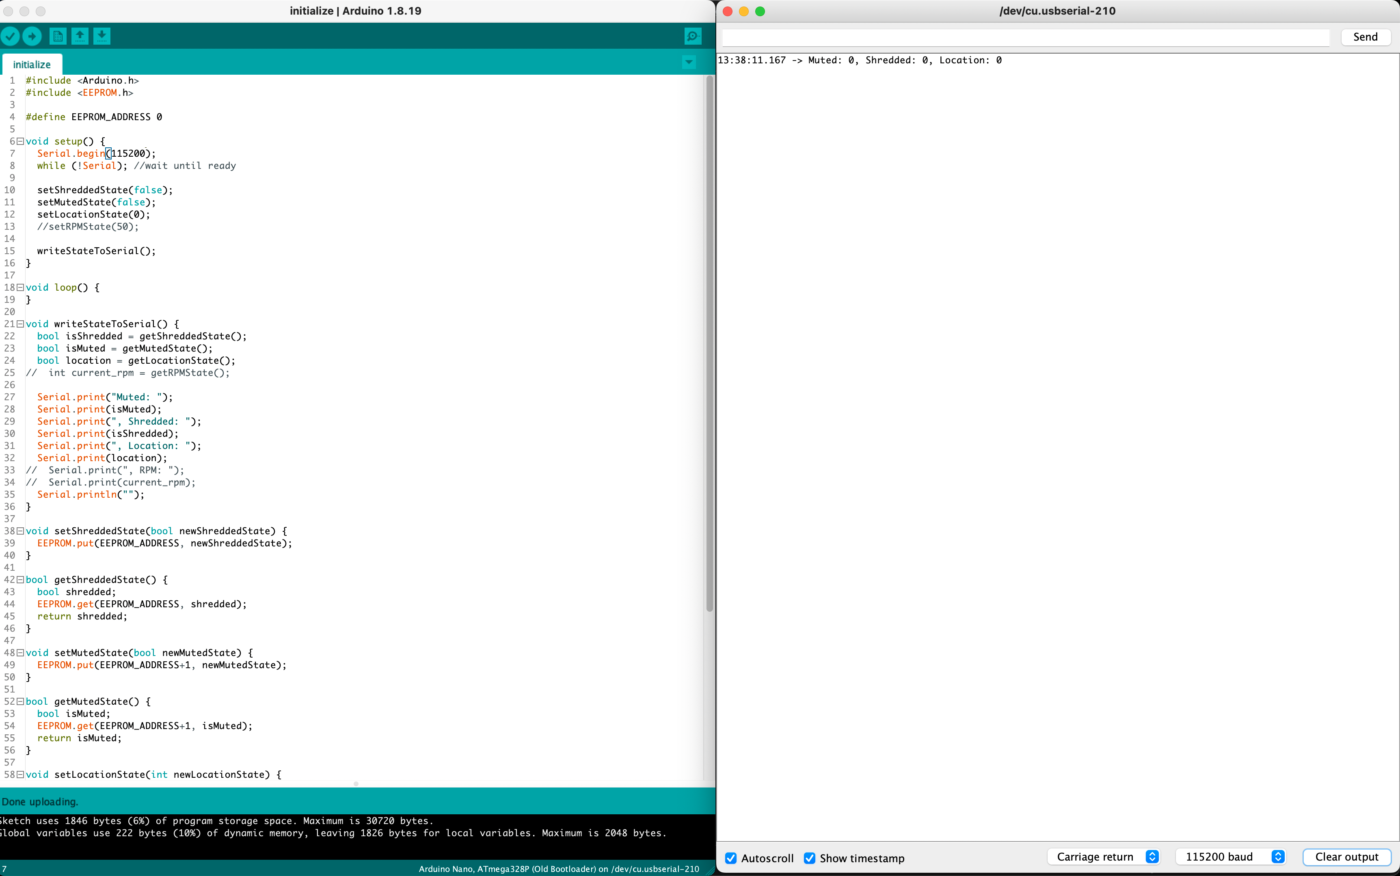
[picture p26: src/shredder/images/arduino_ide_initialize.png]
arduino ide initialize ino

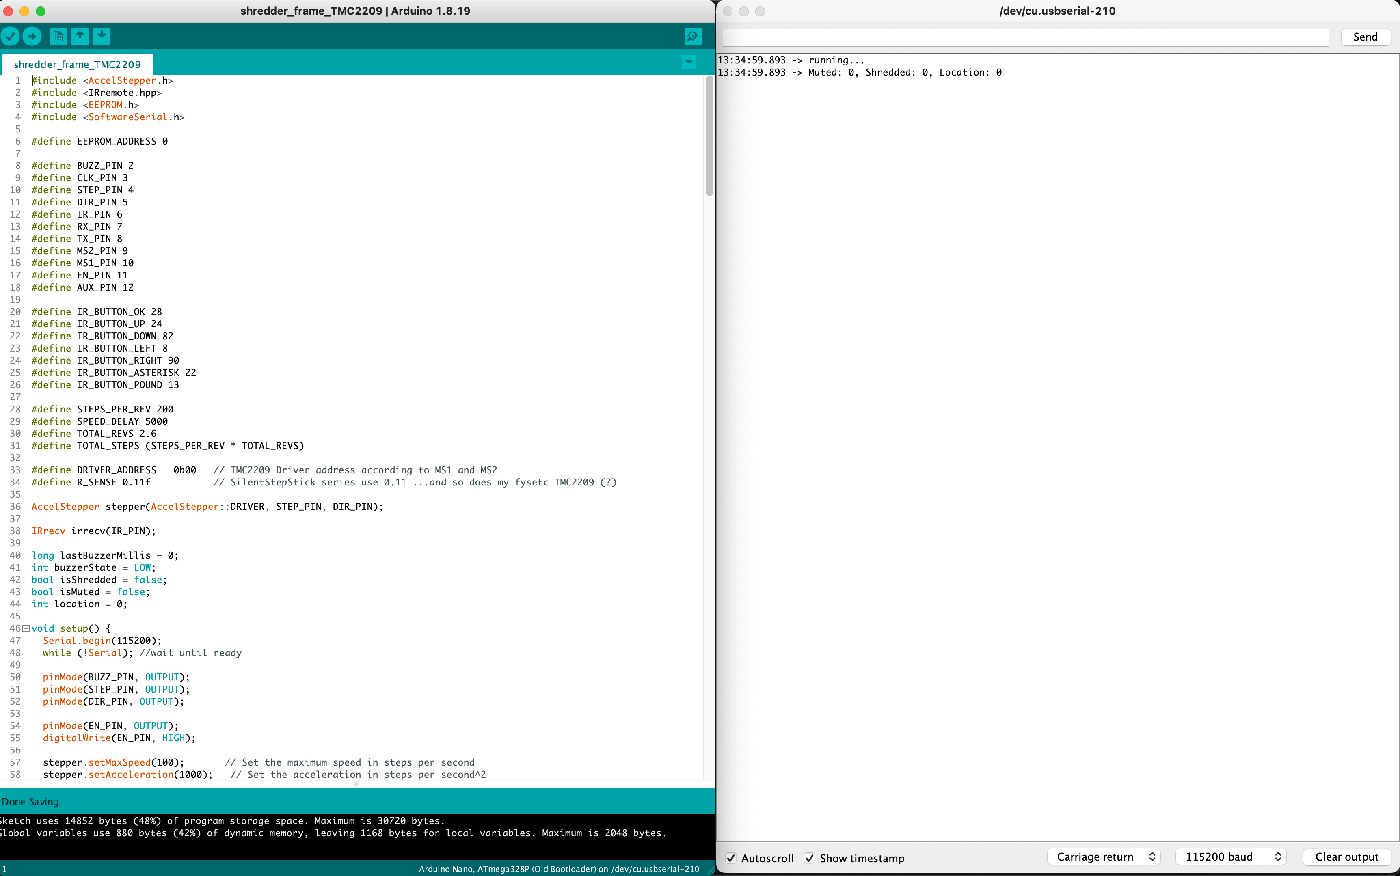
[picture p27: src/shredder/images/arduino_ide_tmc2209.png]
arduino ide tim2209 ino


### Testing
- Leave the USB cable connected so you can see the Serial Monitor output while testing
- Plug the 12V power adapter into the wall and barrel connector
- Point the IR Remote at the IR Receiver and press OK
- The chassis should start moving and beeping, and you should see messages in the Serial Monitor indicating the command received and the action taking place: `runMainSequence`
- Let the main sequence finish.
- Make sure the canvas returned to it's original position.
    - If it slipped while the motor was moving, try adding/removing rubber bands to adjust the tension until it becomes reliable.

## 7. Assemble the fishing line, hanger, and separator.
The fishing line assembly connects the canvas belt to the hanger holding the pre-shredded image and functions as the mechanism for lowering and raising the shredded image hidden within the chassis.

## Tools Required
- Tape (painters or scotch)

## Parts Needed
- Fishing Line
- Swivel Hooks (x2)
- Hanger (3D printed)
- Separator (12x16 art board)

## Steps
- Ensure the canvas belt is positioned so that the artwork is precisely centered for display on the side marked "Front".
- Flip the chassis over so that the side marked "Back" is now facing up
    - The seam on the back of the canvas should be located about a third of the way down on the backside
- Tie one end of the fishing line to one of the swivel hooks. 
    - Ideally, use the knot shown in this [video](https://youtu.be/5vUI_ly1z8k?si=L20prei8CbNu0pxN&t=65)   
- Connect the latching hook part of the swivel hook to the loop located at the seam of the canvas belt. Lock the hook.
- Latch the other swivel hook to the hole on the top of the hanger.
- Thread the open end of the fishing line through the eyelet on the "Top" PCB and through the end of the other swivel hook connected to the hanger.
- Ensuring that the canvas belt has not moved, tie the open end of the fishing line to the other swivel hook in the same fashion as before.
    - The swivel hook and hanger should end up as far up as possible without the swivel hook going through the eyelet at the top.
- Flip the hanger up and over the "Top" piece so it is out of the way for the next step
- Lay the separator art board down across the lateral supports so that it is all the way up as far as it can go. Ensure the cutaway at the top allows the fishing line to pass through unobstructed.
- Secure the separator board using some painters or scotch tape.
- Flip the hanger back down on top of the separator

### 8. Mount the pre-shredded art copy

## Tools Required
- None

## Parts Needed
- Chassis assembly with hanger ready
- Pre-shredded Artwork

## Steps
- Remove the top piece of the hanger and place the pre-shredded artwork onto the hanger so the two prongs go through the two holes at the top of the artwork. 
- Reinstall the top piece of the hanger so that it snaps on and holds the artwork securely.
- Adjust the position of the canvas belt & hanger so they are in their starting position.
- The pre-shredded artwork should NOT hang past the bottom of the chassis when the canvas belt is in the starting position. It should be just above the bottom of the chassis.
- You may need to re-tie the fishing line to adjust the relative positions of the canvas belt and pre-shredded artwork to get it just right.

### 9. Mount to 12 x 16 Picture Frame
Use the included Z-clips to attach the fully assembled chassis to any 12 x 16 wood frame with at least 1.5" wide moulding.

## Tools Required
- Philips screw driver

## Parts Needed
- Z-Clips
- Hanger Wire
- Screws

## Steps
- Be sure to center canvas belt both vertically and horizontally withing the chassis.
- Be sure to center the entire chassis on the picture frame so that everything looks good when viewing from the front.
- Install the Z-Clips using the slots in the side of the chassis
- Install the hanger wire onto the wooden frame. Be sure to hang from the picture frame, not the PCB chassis.
- Picture frame is hung from the wall, PCB chassis it mounted to the picture frame.
- You can optionally install a backing piece if you'd like but this is not necessary.

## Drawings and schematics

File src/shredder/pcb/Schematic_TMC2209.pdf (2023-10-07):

# Arduino

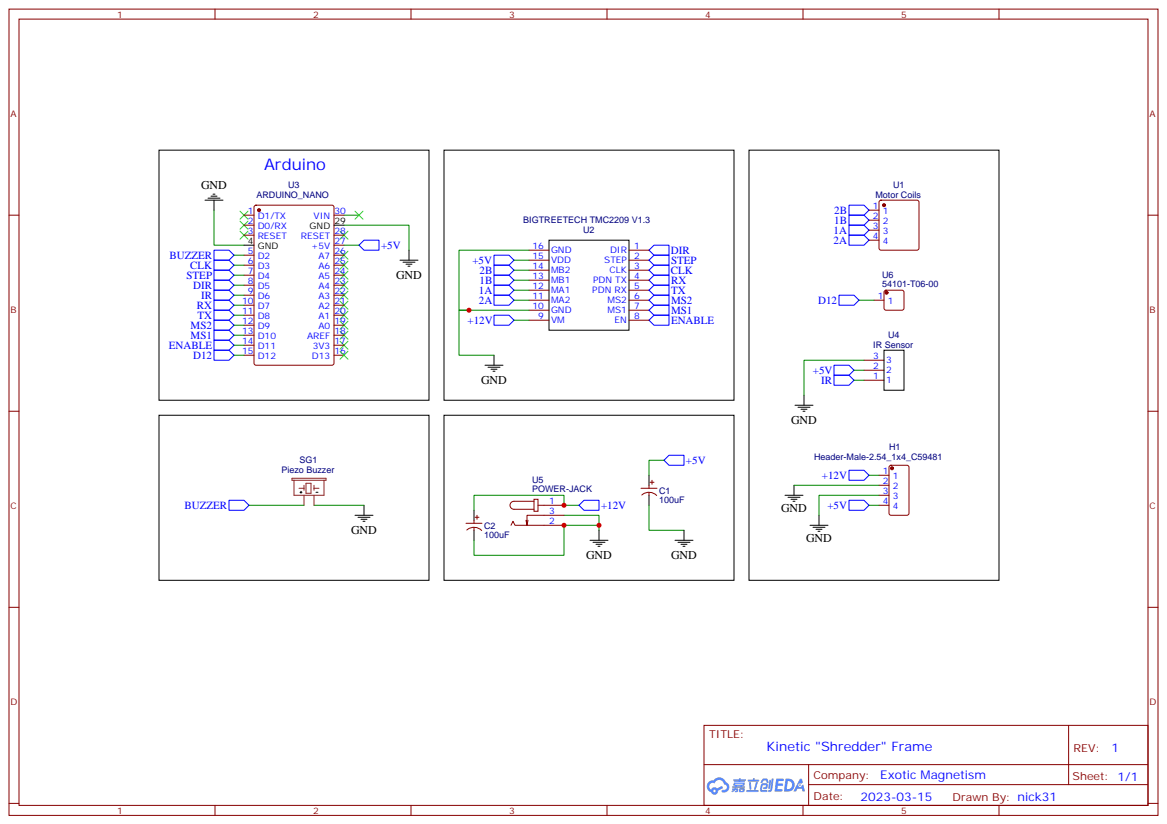
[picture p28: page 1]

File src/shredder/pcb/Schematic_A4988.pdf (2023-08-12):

# Arduino

A4988

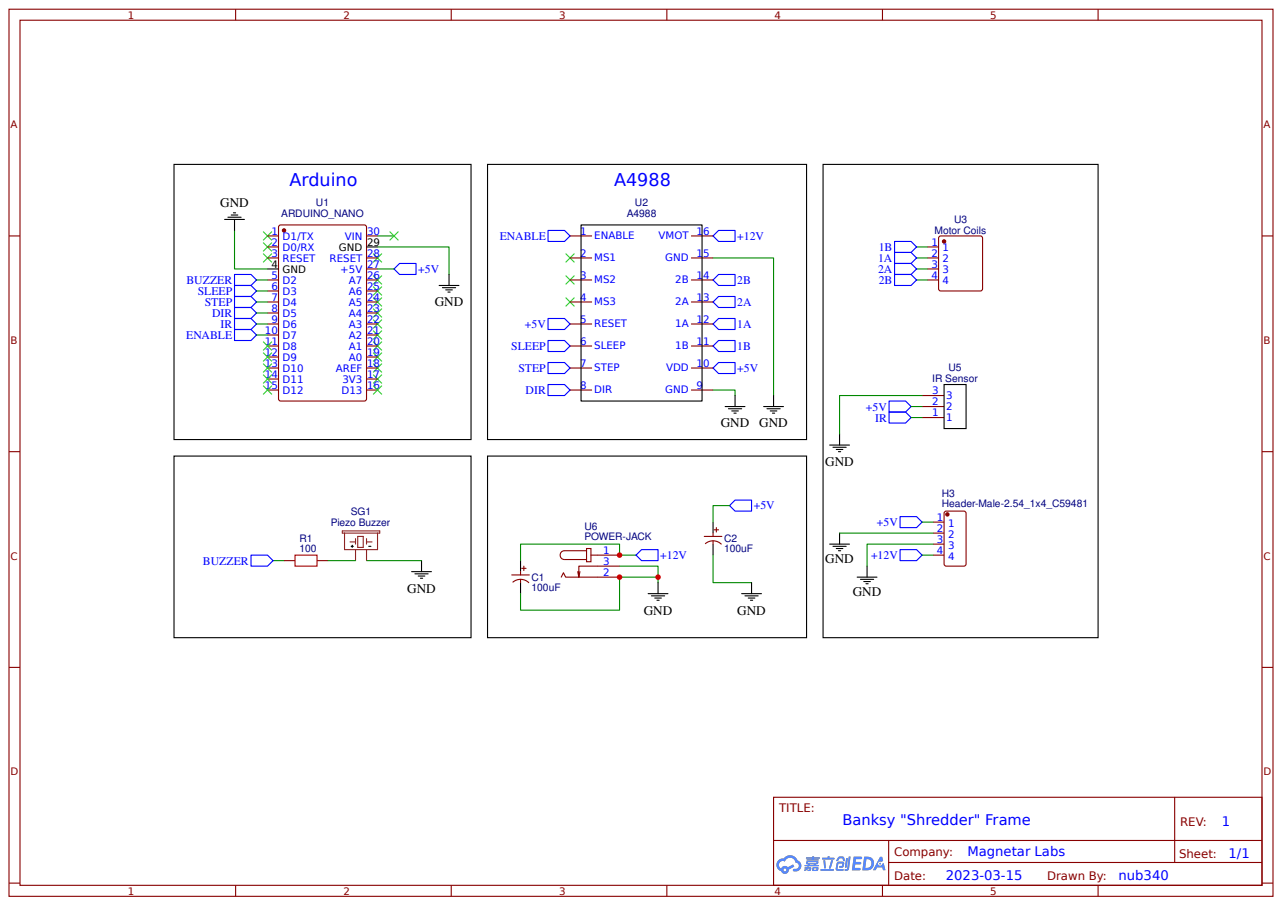
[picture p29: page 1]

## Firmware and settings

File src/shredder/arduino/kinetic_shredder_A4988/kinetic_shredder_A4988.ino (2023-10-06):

#include <Arduino.h>
#include <IRremote.hpp>
#include <EEPROM.h>
#include "BasicStepperDriver.h"

#define EEPROM_ADDRESS 0

// Define stepper motor connections and steps per revolution:
#define BUZZER_PIN 2
#define SLEEP_PIN 3
#define STEP_PIN 4
#define DIR_PIN 5
#define IR_PIN 6
#define EN_PIN 7

#define IR_BUTTON_1 69
#define IR_BUTTON_2 70
#define IR_BUTTON_3 71
#define IR_BUTTON_4 68
#define IR_BUTTON_5 64
#define IR_BUTTON_6 67
#define IR_BUTTON_7 7
#define IR_BUTTON_8 21
#define IR_BUTTON_9 9
#define IR_BUTTON_0 25
#define IR_BUTTON_OK 28
#define IR_BUTTON_UP 24
#define IR_BUTTON_DOWN 82
#define IR_BUTTON_LEFT 8
#define IR_BUTTON_RIGHT 90
#define IR_BUTTON_ASTERISK 22
#define IR_BUTTON_POUND 13

#define STEPS_PER_REV 200
#define RPM_1 10
#define RPM_2 20
#define RPM_3 30
#define RPM_4 40
#define RPM_5 50
#define RPM_6 60
#define RPM_7 70
#define RPM_8 80
#define RPM_9 90
#define RPM_0 100

// 1=full step, 2=half step etc.
#define MICROSTEPS 1
#define SPEED_DELAY_NORMAL 5000
#define SPEED_DELAY_SLOW 10000
#define MOTOR_ACCEL 2000
#define MOTOR_DECEL 1000
#define TOTAL_REVS 2.6
#define TOTAL_STEPS (STEPS_PER_REV * TOTAL_REVS)

BasicStepperDriver stepper(STEPS_PER_REV, DIR_PIN, STEP_PIN, SLEEP_PIN);
//A4988 stepper(STEPS_PER_REV, DIR_PIN, STEP_PIN, SLEEP_PIN, 8, 9, 10);

IRrecv irrecv(IR_PIN);
long lastBuzzerMillis = 0;
int buzzerState = LOW;
bool isShredded = false;
bool isMuted = false;
int location = 0;
int current_rpm = RPM_1;

void setup() {
  Serial.begin(9600);
  while (!Serial); //wait until ready

  stepper.begin(current_rpm, MICROSTEPS);

  isShredded = getShreddedState();
  isMuted = getMutedState();
  location = getLocationState();
  current_rpm = getRPMState();

  pinMode(BUZZER_PIN, OUTPUT);

  IrReceiver.begin(IR_PIN, ENABLE_LED_FEEDBACK);

  Serial.println("Running...");
  if (location > 0){
    Serial.println("Recovering...");
    stepReverse(location, false);
  } else if (location < 0) {
    Serial.println("Recovering...");
    stepForward(abs(location), false);
  }

  Serial.print("Muted: ");
  Serial.print(isMuted);
  Serial.print(", Shredded: ");
  Serial.print(isShredded);
  Serial.print(", Location: ");
  Serial.println(location);
}

void loop() {

  // Returns 0 if no data ready, 1 if data ready.
  if (IrReceiver.decode()) {
    int command = IrReceiver.decodedIRData.command;
    handleIRRemoteCommand(command);
    irrecv.resume();

    Serial.print("Muted: ");
    Serial.print(isMuted);
    Serial.print(", Shredded: ");
    Serial.print(isShredded);
    Serial.print(", Location: ");
    Serial.println(location);
  }
}

void handleIRRemoteCommand(int command) {
  if (command != 0) {
    Serial.print("command: ");
    Serial.print(command);
    Serial.print(" - ");
  }
  switch (command) {
    case IR_BUTTON_UP:
      Serial.println("Trim up");
      stepReverse(10, false);
      break;

    case IR_BUTTON_DOWN:
      Serial.println("Trim down");
      stepForward(10, false);
      break;

    case IR_BUTTON_OK:
      Serial.println("Main sequence");
      runMainSequence();
      break;

    case IR_BUTTON_ASTERISK:
      Serial.println("Reset location");
      resetHomeLocation();
      break;

    case IR_BUTTON_LEFT:
      enterShreddedState();
      break;

    case IR_BUTTON_RIGHT:
      enterNormalState();
      break;

    case IR_BUTTON_POUND:
      toggleMute();
      break;

    case IR_BUTTON_1:
      setRPMState(RPM_1);
      break;

    case IR_BUTTON_2:
      setRPMState(RPM_2);
      break;

    case IR_BUTTON_3:
      setRPMState(RPM_3);
      break;

    case IR_BUTTON_4:
      setRPMState(RPM_4);
      break;    

    case IR_BUTTON_5:
      setRPMState(RPM_5);
      break; 

    case IR_BUTTON_6:
      setRPMState(RPM_6);
      break; 

    case IR_BUTTON_7:
      setRPMState(RPM_7);
      break; 

    case IR_BUTTON_8:
      setRPMState(RPM_8);
      break; 

    case IR_BUTTON_9:
      setRPMState(RPM_9);
      break; 

    case IR_BUTTON_0:
      setRPMState(RPM_0);
      break; 
  }
}

void runMainSequence() {
  Serial.println("runMainSequence");
  
  // Keep track of how long the IR receiver has been stopped
  int startMillis = millis();
  IrReceiver.stop();

  // If already in the shredded state, run the main sequence in reverse
  bool isSequenceReversed = isShredded;
  
  if(isSequenceReversed){
    rotateDegrees(0-TOTAL_STEPS, false);
    //stepReverse(TOTAL_STEPS, false);
    setShreddedState(false);
  } else {
    rotateDegrees(TOTAL_STEPS, true);
    //stepForward(TOTAL_STEPS, true);
    setShreddedState(true);
  }

  Serial.println("Waiting 5 seconds...");
  delay(5000);

  if(isSequenceReversed){
    rotateDegrees(TOTAL_STEPS, true);
    //stepForward(TOTAL_STEPS, true);
    setShreddedState(true);
  } else {
    rotateDegrees(0-TOTAL_STEPS, false);
    //stepReverse(TOTAL_STEPS, false);
    setShreddedState(false);
  }
  
  Serial.println("Waiting 5 seconds...");
  delay(5000);
  Serial.println("Running...");

  // Calculate how long the timer has been stopped. 
  // Start IR receiver again and pass the elapsed time to avoid bug with internal clock.
  int elapsedMicros = (millis() - startMillis) * 1000;
  IrReceiver.start(elapsedMicros);
}

void toggleMute() {
  Serial.println("Toggling mute");
  setMutedState(!isMuted);
  beepOnce();
}

void beepOnce() {
  int startMillis = millis();
  //must stop the IRReceiver as the tone/notone functions need to use the same timer
  IrReceiver.stop(); 
  tone(BUZZER_PIN, 3000);
  delay(500);
  noTone(BUZZER_PIN);
  int elapsedMicros = (millis() - startMillis) * 1000;
  //keep track of how much time has elapsed and use it to restart the IRReceiver
  IrReceiver.start(elapsedMicros); 
}

void resetHomeLocation() {
  setLocationState(0);
  setShreddedState(false);
  beepOnce();
}

void setRpm(int rpm) {
  stepper.stop();
  stepper.begin(rpm, MICROSTEPS);
  setRPMState(rpm);
  beepOnce();
}

void enterShreddedState() {
  if (isShredded) {
    Serial.println("Already shredded");
    return;
  }
  Serial.println("Shredding...");
  int startMillis = millis();
  IrReceiver.stop();
  stepForward(TOTAL_STEPS, true);
  setShreddedState(true);
  int elapsedMicros = (millis() - startMillis) * 1000;
  IrReceiver.start(elapsedMicros);
}

void enterNormalState() {
  if (!isShredded) {
    Serial.println("Already restored");
    return;
  }
  Serial.println("Restoring...");
  int startMillis = millis();
  IrReceiver.stop();
  stepReverse(TOTAL_STEPS, false);
  int elapsedMicros = (millis() - startMillis) * 1000;
  IrReceiver.start(elapsedMicros);
  resetHomeLocation();
}

void rotateDegrees(int deg, bool playBuzzer) {
  stepper.enable();
  stepper.move(deg);
  stepper.disable();
}

void stepForward(int steps, bool playBuzzer) {
  Serial.print("stepForward(");
  Serial.print(steps);
  Serial.println(")");
  digitalWrite(SLEEP_PIN, HIGH);
  digitalWrite(DIR_PIN, HIGH);
  delay(1);

  for (int i = 0; i <= steps; i++) {
    if (playBuzzer) {
      handleBuzzer();
    }
    digitalWrite(STEP_PIN, HIGH);
    delayMicroseconds(SPEED_DELAY_SLOW);
    digitalWrite(STEP_PIN, LOW);
    delayMicroseconds(SPEED_DELAY_SLOW);
  }
  setLocationState(location+steps);
  digitalWrite(SLEEP_PIN, LOW);
  noTone(BUZZER_PIN);
}

void stepReverse(int steps, bool playBuzzer) {
  Serial.print("stepReverse(");
  Serial.print(steps);
  Serial.println(")");
  digitalWrite(SLEEP_PIN, HIGH);
  digitalWrite(DIR_PIN, LOW);
  delay(1);

  for (int i = 0; i <= steps; i++) {
    if (playBuzzer) {
      handleBuzzer();
    }
    digitalWrite(STEP_PIN, HIGH);
    delayMicroseconds(SPEED_DELAY_SLOW);
    digitalWrite(STEP_PIN, LOW);
    delayMicroseconds(SPEED_DELAY_SLOW);
    
  }
  setLocationState(location-steps);
  digitalWrite(SLEEP_PIN, LOW);
  noTone(BUZZER_PIN);
}

void handleBuzzer() {
  if(isMuted) {
    buzzerState = LOW;
    noTone(BUZZER_PIN);
  } else {
    unsigned long currentMillis = millis();
    if (currentMillis - lastBuzzerMillis > 250) {
      lastBuzzerMillis = currentMillis;
      if (buzzerState == LOW) {
        buzzerState = HIGH;
        tone(BUZZER_PIN, 3000);
      }
      else {
        buzzerState = LOW;
        noTone(BUZZER_PIN);
      }
    }
  }
}

void setShreddedState(bool newShreddedState) {
  isShredded = newShreddedState;
  EEPROM.put(EEPROM_ADDRESS, isShredded);
}

bool getShreddedState() {
  bool shredded;
  EEPROM.get(EEPROM_ADDRESS, shredded);
  return shredded;
}

void setMutedState(bool newMutedState) {
  isMuted = newMutedState;
  EEPROM.put(EEPROM_ADDRESS+1, isMuted);
}

bool getMutedState() {
  bool isMuted;
  EEPROM.get(EEPROM_ADDRESS+1, isMuted);
  return isMuted;
}

void setLocationState(int newLocationState) {
  location = newLocationState;
  EEPROM.put(EEPROM_ADDRESS+2, location);
}

int getLocationState() {
  int location;
  EEPROM.get(EEPROM_ADDRESS+2, location);
  return location;
}

void setRPMState(int rpm) {
  current_rpm = rpm;
  EEPROM.put(EEPROM_ADDRESS+2+sizeof(int), rpm);
}

int getRPMState() {
  int rpm;
  EEPROM.get(EEPROM_ADDRESS+2+sizeof(int), rpm);
  return rpm;
}

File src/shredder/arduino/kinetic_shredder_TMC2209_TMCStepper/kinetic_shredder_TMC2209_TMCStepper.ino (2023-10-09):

#include <IRremote.hpp>
#include <EEPROM.h>
#include <TMCStepper.h>
#include <SoftwareSerial.h>

#define EEPROM_ADDRESS 0
#define DRIVER_ADDRESS 0b00 // TMC2209 Driver address according to MS1 and MS2

// Define Arduino pins
#define BUZZ_PIN 2
#define CLK_PIN 3
#define STEP_PIN 4
#define DIR_PIN 5
#define IR_PIN 6
#define RX_PIN 7
#define TX_PIN 8
#define MS2_PIN 9
#define MS1_PIN 10
#define EN_PIN 11
#define AUX_PIN 12

// Define IR remote command codes
#define IR_BUTTON_OK 28
#define IR_BUTTON_UP 24
#define IR_BUTTON_DOWN 82
#define IR_BUTTON_LEFT 8
#define IR_BUTTON_RIGHT 90
#define IR_BUTTON_ASTERISK 22
#define IR_BUTTON_POUND 13

// Define motor parameters
#define STEPS_PER_REV 200
#define MAX_CURRENT 1000
#define R_SENSE 0.11f
#define MICROSTEPS  4 // Set the microstepping mode (1, 2, 4, 8, 16)
#define SPEED_DELAY 8000 / MICROSTEPS
#define TOTAL_REVS 2.6
#define TOTAL_STEPS (STEPS_PER_REV * TOTAL_REVS) * MICROSTEPS
#define TRIM_STEPS 20 

// Instantiate classes
IRrecv irrecv(IR_PIN);
SoftwareSerial SoftSerial(RX_PIN, TX_PIN);
TMC2209Stepper driver(&SoftSerial, R_SENSE, DRIVER_ADDRESS);

// Initialize global variables
long _lastBuzzerMillis = 0;
long _irrecvPausedAtMillis = 0;
int _buzzerState = LOW;
bool _isShredded = false;
bool _isMuted = false;
int _location = 0;

/**
 * Runs once per restart to setup the device and starting state
 */
void setup() {
  Serial.begin(115200);
  while (!Serial); //wait until ready
  SoftSerial.begin(115200);
  driver.beginSerial(115200);

  pinMode(BUZZ_PIN, OUTPUT);
  pinMode(STEP_PIN, OUTPUT);
  pinMode(DIR_PIN, OUTPUT);
  pinMode(EN_PIN, OUTPUT);
  digitalWrite(EN_PIN, LOW);  // Enable driver (LOW means Enable)

  IrReceiver.begin(IR_PIN, ENABLE_LED_FEEDBACK);

  driver.begin();                 
  driver.rms_current(MAX_CURRENT); 
  driver.microsteps(MICROSTEPS);
  driver.toff(4);
  driver.en_spreadCycle(false);
  driver.pwm_autoscale(true); // Needed for stealthChop

  _isShredded = getShreddedState();
  _isMuted = getMutedState();
  _location = getLocationState();

  Serial.println("Running...");
  writeStateToSerial();
}

/**
 * The main loop.
 */
void loop() {

  // Returns 0 if no data ready, 1 if data ready.
  if (IrReceiver.decode()) {
    int command = IrReceiver.decodedIRData.command;
    handleIRRemoteCommand(command);
    irrecv.resume();

    writeStateToSerial();
  }
}

/**
 * handleIRRemoteCommand
 * 
 * Handles the IR remote commands
 */
void handleIRRemoteCommand(int command) {
  Serial.print("command: ");
  Serial.print(command);
  Serial.print(" - ");
  if (command == 0) {
    Serial.println("undefined");
  } else {
    switch (command) {
      case IR_BUTTON_UP:
        Serial.println("Trim up");
        stepReverse(TRIM_STEPS, false);
        break;
  
      case IR_BUTTON_DOWN:
        Serial.println("Trim down");
        stepForward(TRIM_STEPS, false);
        break;
  
      case IR_BUTTON_OK:
        Serial.println("Main sequence");
        runMainSequence();
        break;
  
      case IR_BUTTON_ASTERISK:
        Serial.println("Reset location");
        resetLocationState();
        break;
  
      case IR_BUTTON_LEFT:
        enterShreddedState();
        break;
  
      case IR_BUTTON_RIGHT:
        enterNormalState();
        break;
  
      case IR_BUTTON_POUND:
        toggleMute();
        break;
    }
  }
}

/**
 * runMainSequence
 * 
 * Executes the main sequence normally, or in reverse, 
 * depending on the current shredded state.
 */
void runMainSequence() {
  Serial.println("runMainSequence");

  stopIRReceiver();

  // If already in the shredded state, run the main sequence in reverse
  bool isSequenceReversed = _isShredded;
  
  if(isSequenceReversed){
    stepReverse(TOTAL_STEPS, false);
    setShreddedState(false);
  } else {
    stepForward(TOTAL_STEPS, true);
    setShreddedState(true);
  }

  Serial.println("Waiting 5 seconds...");
  delay(5000);

  if(isSequenceReversed){
    stepForward(TOTAL_STEPS, true);
    setShreddedState(true);
  } else {
    stepReverse(TOTAL_STEPS, false);
    setShreddedState(false);
  }
  
  Serial.println("Waiting 3 seconds...");
  delay(3000);
  Serial.println("Running...");

  startIRReceiver();
}

/**
 * toggleMute
 * 
 * Toggles the mute feature on/off
 */
void toggleMute() {
  Serial.println("Toggling mute");
  setMutedState(!_isMuted);
  stopIRReceiver();
  tone(BUZZ_PIN, 3000);
  delay(500);
  noTone(BUZZ_PIN);
  startIRReceiver();
}

/**
 * resetLocationState
 * 
 * Resets the location state to zero
 */
void resetLocationState() {
  setLocationState(0);
}

/**
 * enterShreddedState
 * 
 * Puts the device into the "shredded" state
 */
void enterShreddedState() {
  if (_isShredded) {
    Serial.println("Already shredded");
    return;
  }
  Serial.println("Shredding...");
  stopIRReceiver();
  stepForward(TOTAL_STEPS, true);
  setShreddedState(true);
  startIRReceiver();
}

/**
 * enterNormalState
 * 
 * Puts the device into the "normal" state
 */
void enterNormalState() {
  if (!_isShredded) {
    Serial.println("Already restored");
    return;
  }
  Serial.println("Restoring...");
  stopIRReceiver();
  stepReverse(TOTAL_STEPS, false);
  setShreddedState(false);
  startIRReceiver();
}

/**
 * stepForward
 * 
 * Sets the stepper motor direction and calls stepAndBuzz
 */
void stepForward(int steps, bool playBuzzer) {
  Serial.print("stepForward(");
  Serial.print(steps);
  Serial.println(")");
  driver.shaft(false);
  delay(1);

  stepAndBuzz(steps, playBuzzer);
}

/**
 * stepReverse
 * 
 * Sets the stepper motor direction and calls stepAndBuzz
 */
void stepReverse(int steps, bool playBuzzer) {
  Serial.print("stepReverse(");
  Serial.print(steps);
  Serial.println(")");
  driver.shaft(true);
  delay(1);

  stepAndBuzz(steps, playBuzzer);
}

/**
 * stepAndBuzz
 * 
 * Sends the commands to the stepper motor and piezo buzzer
 * according to the parameters passed
 */
void stepAndBuzz(int steps, bool playBuzzer) {
  for (int i = 0; i <= steps; i++) {
    if (playBuzzer) {
      handleBuzzer();
    }
    digitalWrite(STEP_PIN, HIGH);
    delayMicroseconds(SPEED_DELAY);
    digitalWrite(STEP_PIN, LOW);
    delayMicroseconds(SPEED_DELAY);
  }
  setLocationState(_location-steps);
  noTone(BUZZ_PIN);
}

/**
 * stopIRReceiver
 * 
 * Captures millis when reciever was stopped.
 */
void stopIRReceiver() {
  _irrecvPausedAtMillis = millis();
  IrReceiver.stop();
}

/*
 * startIRReceiver
 * 
 * Calculates the elapsed millis since the IRReceiver was stopped.
 * Starts IR receiver again and passes the elapsed time to avoid an issue with the internal clock.
 * This took me weeks to figure out! The remote would only work once per restart...
*/
void startIRReceiver() {
  int elapsedMicros = (millis() - _irrecvPausedAtMillis) * 1000;
  IrReceiver.start(elapsedMicros);
}
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

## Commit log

2023-10-04 assembly instructions
2023-10-07 stl (#5)
    [90degree-jig2.stl, hanger.stl, motor-mount.stl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]
2023-10-09 V1 (#6)
    * stl
    * stepper motor impls
    * codez
    * remove non functioning code
2023-10-09 V1 (#7)
    * comments
    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
2023-10-11 V1 (#8)
    * license
    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
